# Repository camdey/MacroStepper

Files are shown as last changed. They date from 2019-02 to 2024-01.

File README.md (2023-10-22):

# MacroStepper v3.0
Author: Cam Dey

Created: 2018-12-18

v2.0: 2020-01-01

v3.0: 2023-10-11 // refactor, introduces breaking changes

The MacroStepper is a fully automated macrophotography rig designed to enable a camera to take photos at precisely incremented steps. The macroStack can work with or without an automated shutter and also in manual mode if the user prefers to control the stepping themselves.

# Schematic
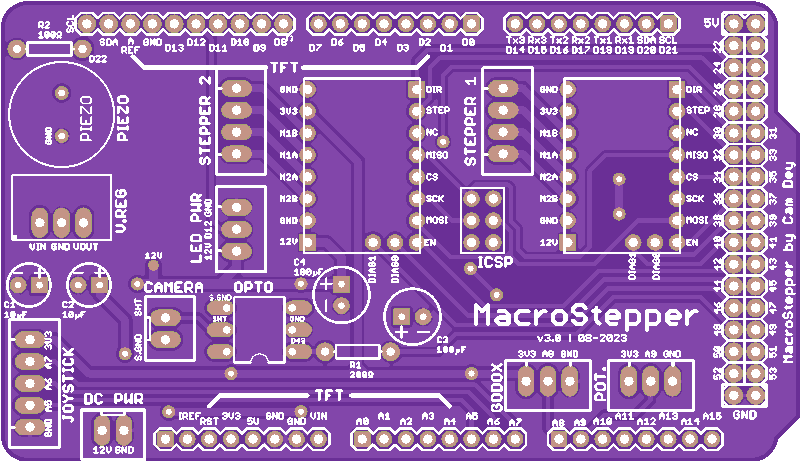
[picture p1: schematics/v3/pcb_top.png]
PCB_top

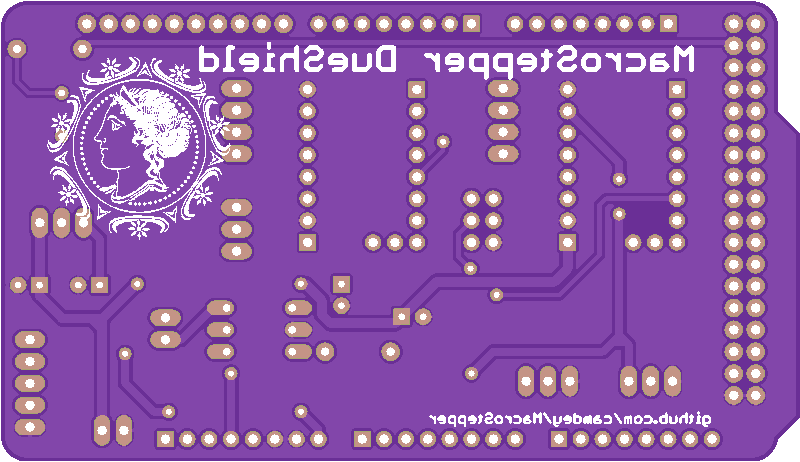
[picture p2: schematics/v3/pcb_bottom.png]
PCB_bottom


# Interface
**Home Screen**
 - House icon: _run homing sequence for the rail, finds min and max positions of the rail_
 - X icon: _clears the settings from the auto mode_
 
**Manual Screen**
 - Step Dist: _press to set distance per movement of the motor_
	 - _value is the distance per movement covered by the rail in millimetres_
 - Step Nr: _number of movements taken in manual mode_
 - Rail Pos: _current position of the camera on the rail_
 - Aperture icon: _press to enable/disable automated shutter_
 - X icon: _press to clear step count_
 - Arrows: _for increment/decrementing the Step Size if enabled or moving the rail forward/back otherwise_

**Auto Screen**
 - Step Dist: _press to set distance per movement of the motor_
	 - _value is the distance per movement covered by the rail in millimetres_
 - Est. Time: _estimated time remaining in autoStack procedure. Takes into account shutter delay and the recycle time of the flash unit_
 - Progress: _number of movements completed out of total number of movements in procedure_
 - Aperture icon: _press to enable/disable automated shutter_
 - Cog icon: _opens the config menu for the auto mode_
 - Play symbol: _used to increment Step Size if enabled, otherwise used for starting the autoStack procedure_
 - Pause symbol: _used to decrement Step Size if enabled, otherwise used for pausing the autoStack procedure_

**Config Screen**

 - START: _press to set the start position for the autoStack procedure. Will automatically change to current position when enabled, use joystick or arrows to move rail into correct position_
 - END: _press to set the end position for the autoStack procedure. Will automatically change to current position when enabled, use joystick or arrows to move rail into correct position_
 - RUN: _will move the camera rail to the START position, slowly increment through the autoStack range until it reaches the END, and then move back to the START position_
 - Clock symbol: _press to change the shutter delay between taking photos after each movement of the stepper motor_
 - Arrows: _used to increment/decrement shutter delay or move the position of the rail_

# Functionality
**Flash/Shutter Control**
The camera shutter is controlled by the Arduino via cable where a HIGH signal is sent to a transistor to short the Shutter and Focus pins of the Sony A6000 to ground. The duration of this signal is determined by an output signal from a PC sync cable. This cable is connected to the output of a Godox X1T-S transmitter. This transmitter sends a LOW signal for several milliseconds when the flash is ready to trigger. When the low signal is received by the Arduino, the shutter line goes LOW and the Shutter and Focus pins are returned to nominal state.

**Distance settings**
The step distance setting refers to the distance travelled by the rail per movement. A movement is the sequence of steps required by the stepper motor to travel the set distance. The default distance per step in my case was 25μm, calculated by the following: screw pitch / steps per revolution / gear reduction. My rail had a 1mm pitch and 1:2 gear reduction, while the motor takes 200 steps per revolution.

If the step size is set to 100μm, this equates to four steps at 25μm each. The sequence of these four steps is termed a movement in this project.

**AutoStack Procedure**
The autoStack procedure will increment a range by a given number of movements, determined by the step distance and the start and end positions determined by the user. With a 100μm step distance and 180 steps required to go from the start position to the end position, 45 (180/4) movements are required and thus 45 photos will be taken. The procedure can be paused or reset at any stage and after completion the procedure can be restarted. Both step distance and the end position can be changed during the procedure once paused.

# Macrophotography

## What is focus stacking?

Focus stacking is a method popular within the field of macrophotography where multiple photos of the same subject are taken at different focus depths and then merged together with software. This enables a macro lens with a shallow depth of field to produce an image of a subject that is fully in focus, even if the subject is physically longer than the depth of field of the lens.

## What do you need for Macrophotography?

While you can create a focus stack just with handheld photos taken at different distances from the subject, typically a **macro rail** is used to help with this process. A macro rail allows you to move a camera attached to a platform by very specific distances along a fixed rail or slide. By turning a handle or knob of the macro rail, the camera can be incremented along the rail by distances as small as 25μm or as large as the rail is long.

**Macro Rail**
For this project, you will need a macro rail that can be attached to a stepper motor. Many commercially available macro rails can be retrofitted with a pinion gear to accept a belt, which is in turn attached to a pinion gear on a stepper motor. Other macro rails are designed to interface directly with a stepper motor, especially those designed to be used for CNC machines or 3D printing.

**Stepper Motor**
A stepper motor is required to move the macro rail automatically. You can do this manually, and many do, but after awhile you get sick of the repetitive process of "move camera rail, take photo, move camera rail, take photo".

There are many types of stepper motors available but for this project I would recommend one in the NEMA 17 form factor with either 200 (1.8°) or 400 (0.9°) steps per revolution and between 1A and 2A current rating. The current rating is important for the load the stepper motor can move and hold but it is not the only determiner of this. A motor with a holding torque of at least 3kg-cm should be adequate.

The voltage of the motor is less important as you can supply more voltage than the rated voltage of the motor. More supply voltage typically equals a faster motor.

**Camera and Lens**
Any DSLR or mirrorless camera will be suitable. A macro lens of your choosing is also sufficient.

**Lighting**
I would recommend buying a flash for your camera, preferably wireless. Macrophotography often deals with very low amounts of light and high apertures so a flash is particularly useful. This project is designed to work with the shutter of a Sony multi-terminal port for triggering the shutter and a PC sync cable for detecting the output signal of the flash being triggered but either of these can be changed to the communication methods required for your camera and flash.

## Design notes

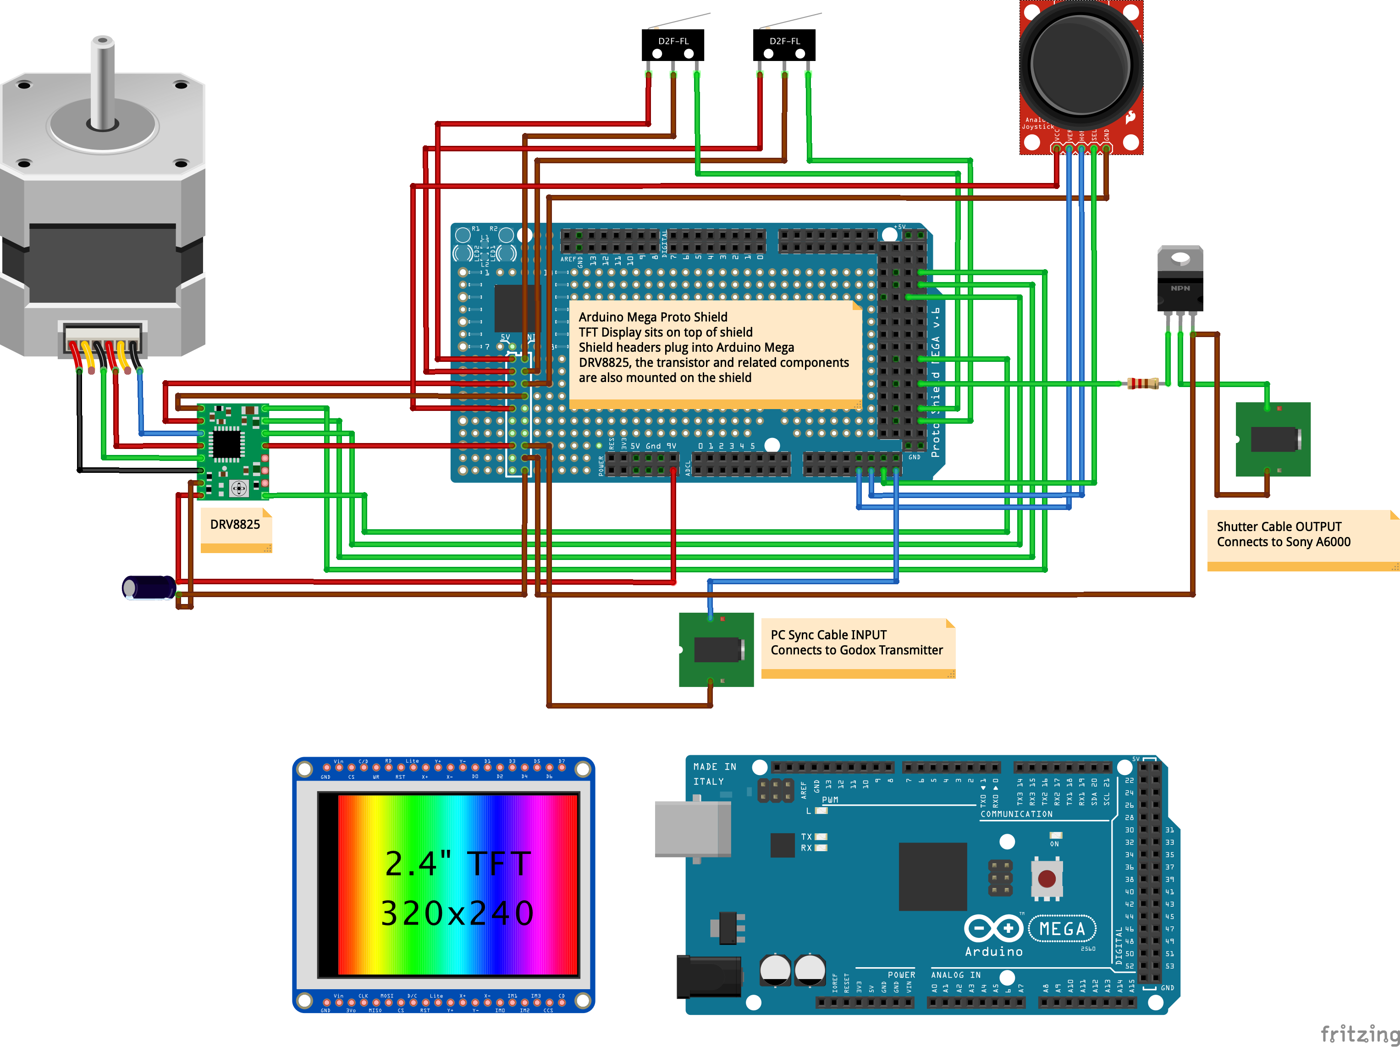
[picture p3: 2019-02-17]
MacroStepper_schematic.png

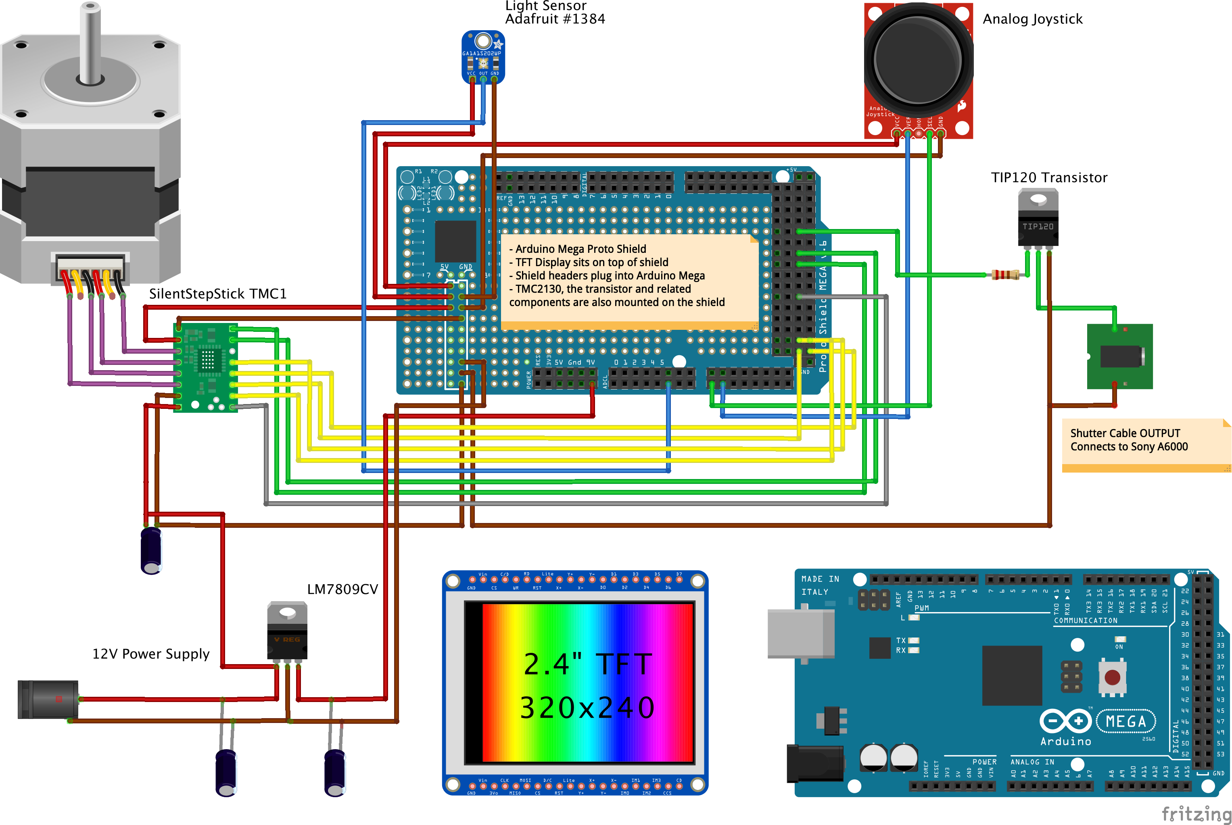
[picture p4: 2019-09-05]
MacroStepper Schematic [Update].png

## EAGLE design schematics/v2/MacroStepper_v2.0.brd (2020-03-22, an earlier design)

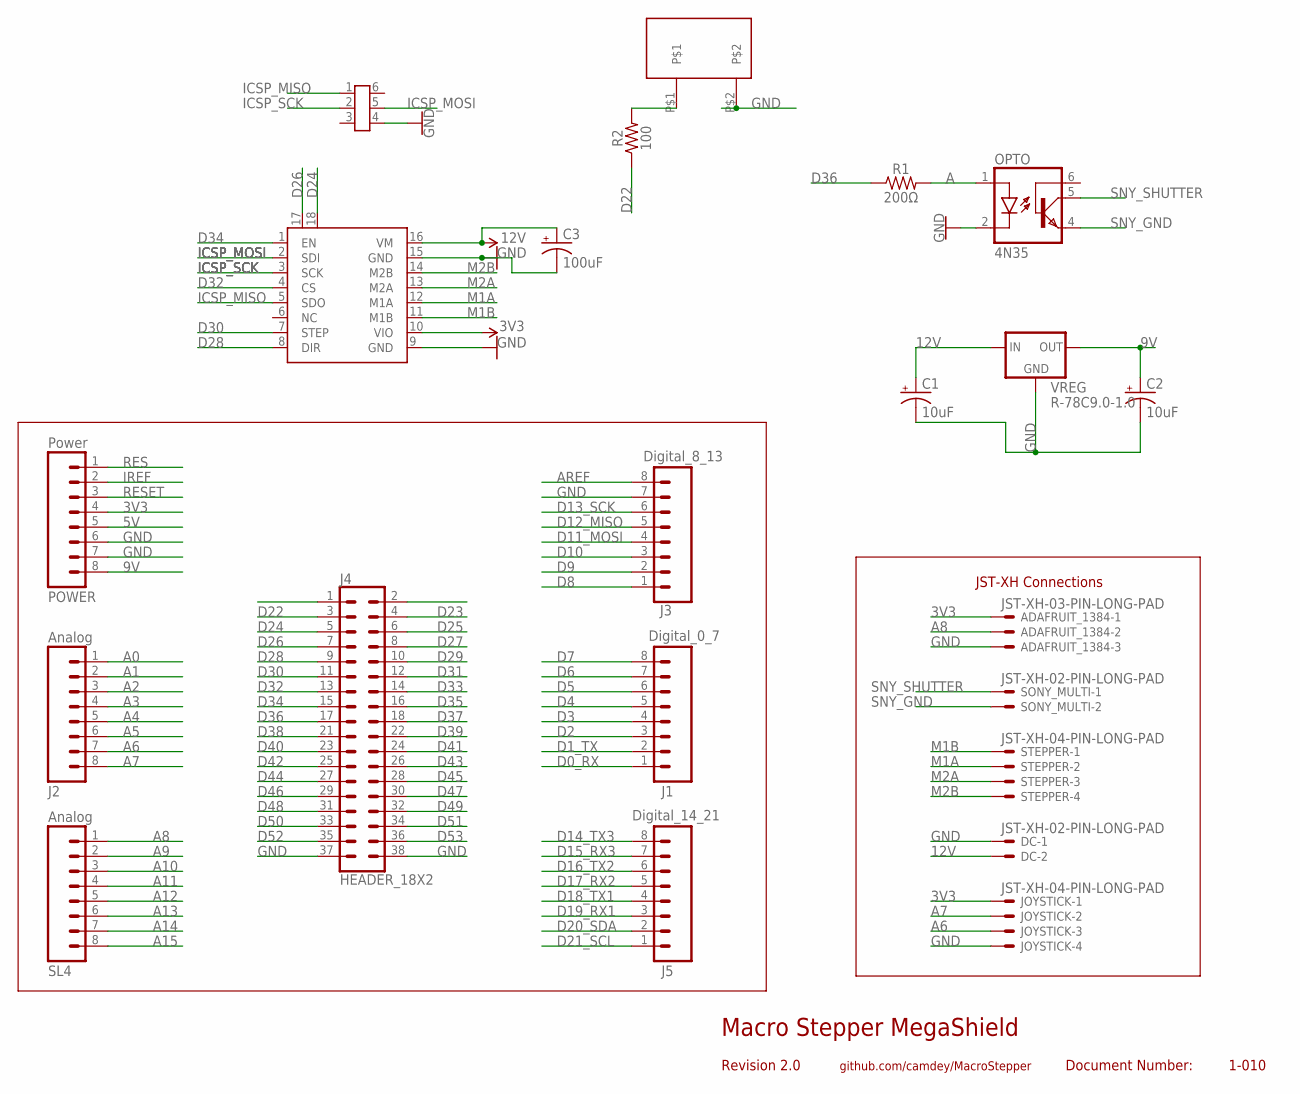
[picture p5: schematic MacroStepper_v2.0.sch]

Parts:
ADAFRUIT_1384: JST-XH-03-PIN-LONG-PAD; JST-XH-03-PACKAGE-LONG-PAD
C1, C2: 10uF; CPOL-RADIAL-2.5MM-5MM
C3: 100uF; CPOL-RADIAL-2.5MM-6.5MM
DC: JST-XH-02-PIN-LONG-PAD; JST-XH-02-PACKAGE-LONG-PAD
ICSP: MEGA_ICSP
J1: Digital_0_7; 1X08
J2: Analog; 1X08
J3: Digital_8_13; 1X08
J4: HEADER_18X2; 2X18
J5: Digital_14_21; 1X08
JOYSTICK: JST-XH-04-PIN-LONG-PAD; JST-XH-04-PACKAGE-LONG-PAD
OPTO: 4N35; DIL06
PIEZO: PS1240P02BT
POWER: Power; 1X08
R1: 200Ω; AXIAL-0.3
R2: 100; AXIAL-0.3
SL4: Analog; 1X08
SONY_MULTI: JST-XH-02-PIN-LONG-PAD; JST-XH-02-PACKAGE-LONG-PAD
STEPPER: JST-XH-04-PIN-LONG-PAD; JST-XH-04-PACKAGE-LONG-PAD
TMC2130: TMC2130; DIL16
VREG: R-78C9.0-1.0; SIP3

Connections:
3V3: ADAFRUIT_1384.1, JOYSTICK.1, POWER.4, TMC2130.10 (VIO)
5V: POWER.5
9V: C2.1 (+), POWER.8, VREG.3 (OUT)
12V: C1.1 (+), C3.1 (+), DC.2, TMC2130.16 (VM), VREG.1 (IN)
A: OPTO.1 (A), R1.P$2 (2)
A0: J2.1
A1: J2.2
A2: J2.3
A3: J2.4
A4: J2.5
A5: J2.6
A6: J2.7, JOYSTICK.3
A7: J2.8, JOYSTICK.2
A8: ADAFRUIT_1384.2, SL4.1
A9: SL4.2
A10: SL4.3
A11: SL4.4
A12: SL4.5
A13: SL4.6
A14: SL4.7
A15: SL4.8
AREF: J3.8
D0_RX: J1.1
D1_TX: J1.2
D2: J1.3
D3: J1.4
D4: J1.5
D5: J1.6
D6: J1.7
D7: J1.8
D8: J3.1
D9: J3.2
D10: J3.3
D11_MOSI: J3.4
D12_MISO: J3.5
D13_SCK: J3.6
D14_TX3: J5.8
D15_RX3: J5.7
D16_TX2: J5.6
D17_RX2: J5.5
D18_TX1: J5.4
D19_RX1: J5.3
D20_SDA: J5.2
D21_SCL: J5.1
D22: J4.3 (D22), R2.P$1 (1)
D23: J4.4 (D23)
D24: J4.5 (D24), TMC2130.18 (DIAG1)
D25: J4.6 (D25)
D26: J4.7 (D26), TMC2130.17 (DIAG0)
D27: J4.8 (D27)
D28: J4.9 (D28), TMC2130.8 (DIR)
D29: J4.10 (D29)
D30: J4.11 (D30), TMC2130.7 (STEP)
D31: J4.12 (D31)
D32: J4.13 (D32), TMC2130.4 (CS)
D33: J4.14 (D33)
D34: J4.15 (D34), TMC2130.1 (EN)
D35: J4.16 (D35)
D36: J4.17 (D36), R1.P$1 (1)
D37: J4.18 (D37)
D38: J4.21 (D38)
D39: J4.22 (D39)
D40: J4.23 (D40)
D41: J4.24 (D41)
D42: J4.25 (D42)
D43: J4.26 (D43)
D44: J4.27 (D44)
D45: J4.28 (D45)
D46: J4.29 (D46)
D47: J4.30 (D47)
D48: J4.31 (D48)
D49: J4.32 (D49)
D50: J4.33 (D50)
D51: J4.34 (D51)
D52: J4.35 (D52)
D53: J4.36 (D53)
GND: ADAFRUIT_1384.3, C1.2 (-), C2.2 (-), C3.2 (-), DC.1, ICSP.4 (GND), J3.7, J4.37 (GND), J4.38 (GND), JOYSTICK.4, OPTO.2 (C), PIEZO.P$2, POWER.6, POWER.7, TMC2130.9 (GND), TMC2130.15 (GND), VREG.2 (GND)
ICSP_MISO: ICSP.1 (MISO), TMC2130.5 (SDO)
ICSP_MOSI: ICSP.5 (MOSI), TMC2130.2 (SDI)
ICSP_SCK: ICSP.2 (SCK), TMC2130.3 (SCK)
IREF: POWER.2
M1A: STEPPER.2, TMC2130.12 (M1A)
M1B: STEPPER.1, TMC2130.11 (M1B)
M2A: STEPPER.3, TMC2130.13 (M2A)
M2B: STEPPER.4, TMC2130.14 (M2B)
unnamed: PIEZO.P$1, R2.P$2 (2)
RES: POWER.1
RESET: POWER.3
SNY_GND: OPTO.4 (EMI), SONY_MULTI.2
SNY_SHUTTER: OPTO.5 (COL), SONY_MULTI.1

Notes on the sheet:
JST-XH Connections
Macro Stepper MegaShield
Revision 2.0
github.com/camdey/MacroStepper
Document Number:
1-010

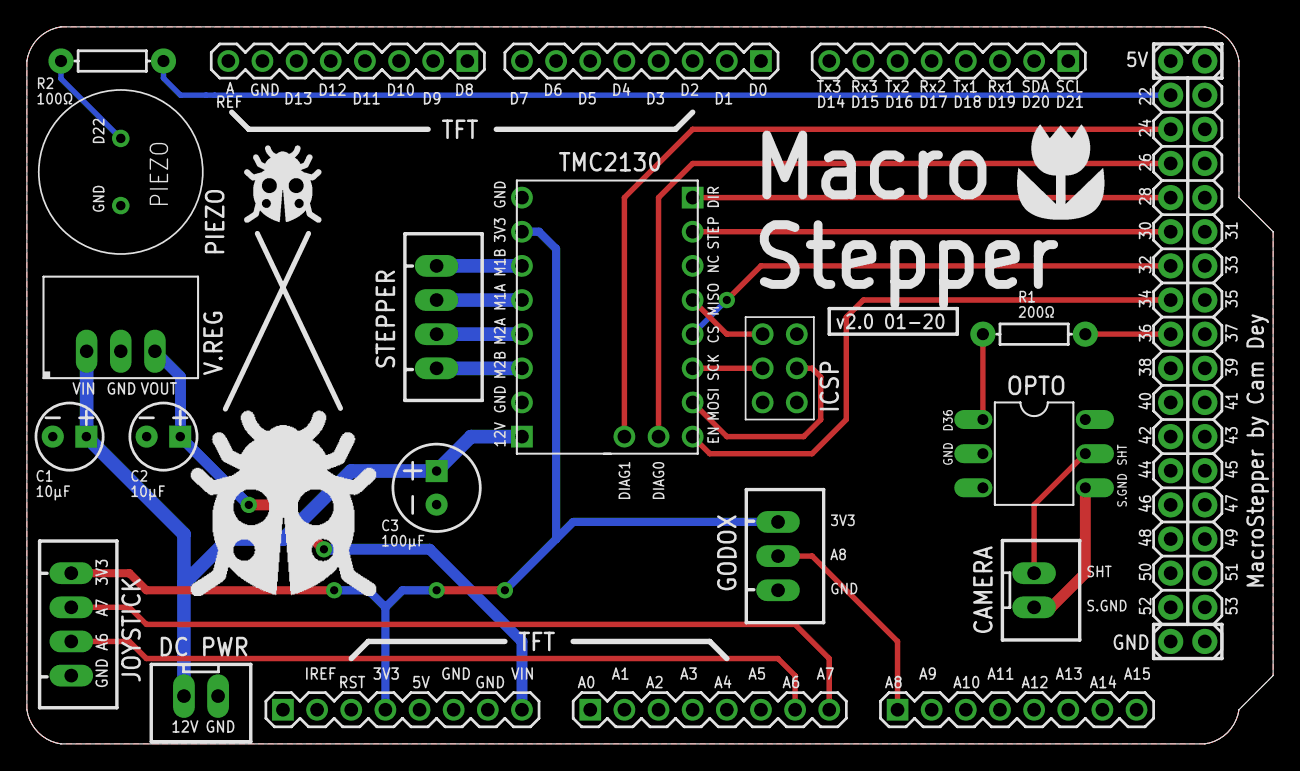
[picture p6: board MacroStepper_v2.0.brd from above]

Board: 2 copper layers, 92.7 x 53.3 mm, 22 parts (0 on the bottom side), 26 nets.

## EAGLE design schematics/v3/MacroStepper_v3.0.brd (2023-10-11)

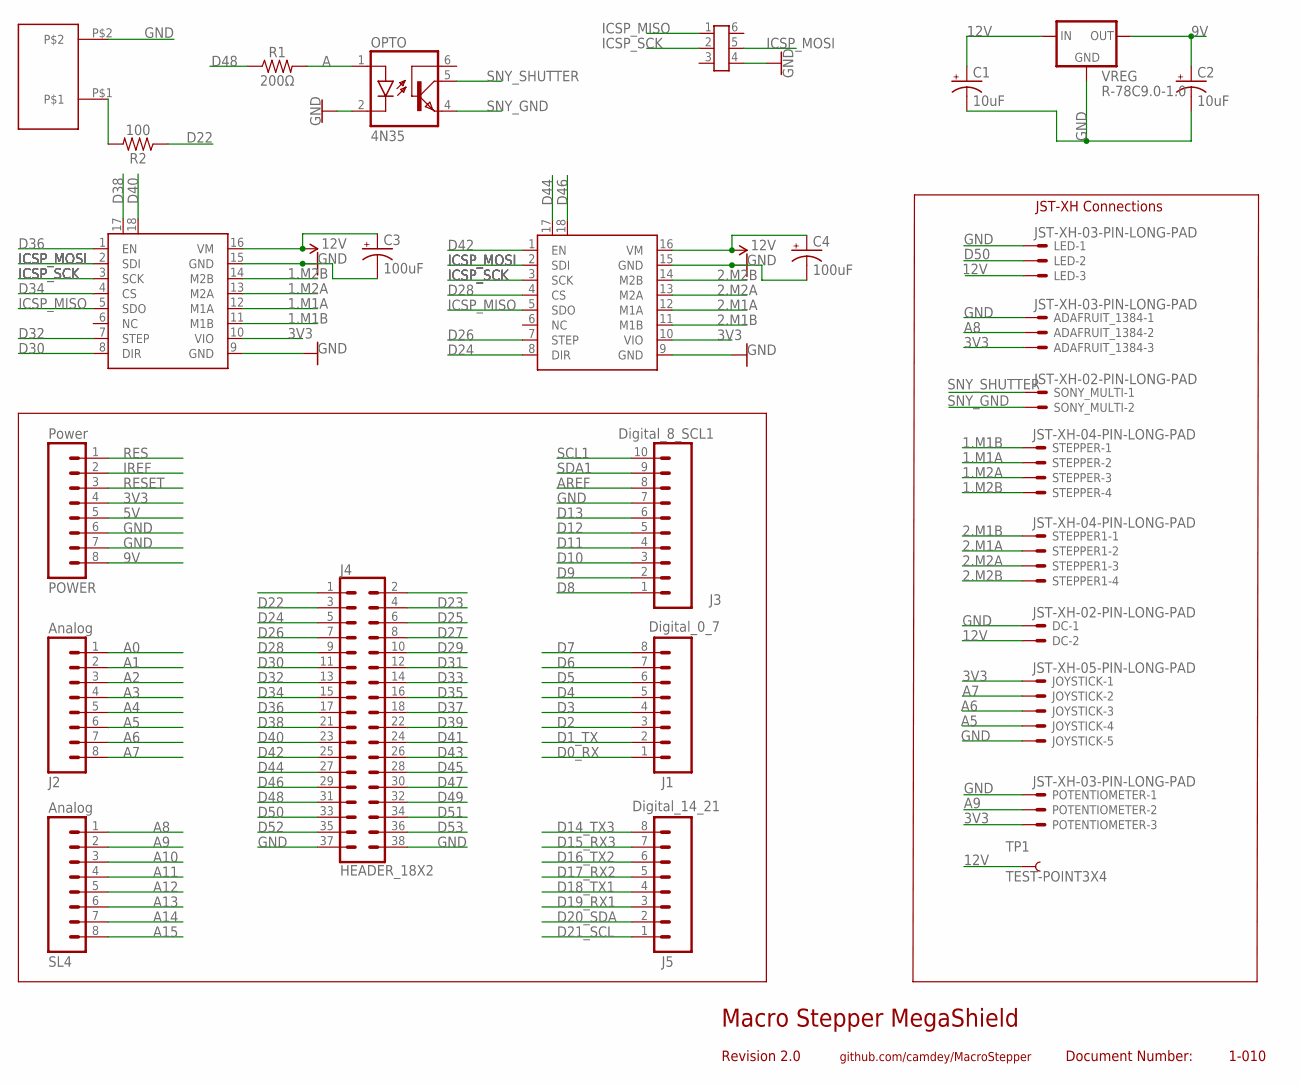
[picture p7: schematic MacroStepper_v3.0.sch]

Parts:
ADAFRUIT_1384: JST-XH-03-PIN-LONG-PAD; JST-XH-03-PACKAGE-LONG-PAD
C1, C2: 10uF; CPOL-RADIAL-2.5MM-5MM
C3, C4: 100uF; CPOL-RADIAL-2.5MM-6.5MM
DC: JST-XH-02-PIN-LONG-PAD; JST-XH-02-PACKAGE-LONG-PAD
ICSP: MEGA_ICSP
J1: Digital_0_7; 1X08
J2: Analog; 1X08
J3: Digital_8_SCL1; 1X10
J4: HEADER_18X2; 2X18
J5: Digital_14_21; 1X08
JOYSTICK: JST-XH-05-PIN-LONG-PAD; JST-XH-05-PACKAGE-LONG-PAD
LED: JST-XH-03-PIN-LONG-PAD; JST-XH-03-PACKAGE-LONG-PAD
OPTO: 4N35; DIL06
PIEZO: PS1240P02BT
POTENTIOMETER: JST-XH-03-PIN-LONG-PAD; JST-XH-03-PACKAGE-LONG-PAD
POWER: Power; 1X08
R1: 200Ω; AXIAL-0.3
R2: 100; AXIAL-0.3
SL4: Analog; 1X08
SONY_MULTI: JST-XH-02-PIN-LONG-PAD; JST-XH-02-PACKAGE-LONG-PAD
STEPPER, STEPPER1: JST-XH-04-PIN-LONG-PAD; JST-XH-04-PACKAGE-LONG-PAD
TMC5160_1, TMC5160_2: TMC2130; DIL16
TP1: TEST-POINT3X4; PAD.03X.04
VREG: R-78C9.0-1.0; SIP3

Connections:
1.M1A: STEPPER.2, TMC5160_1.12 (M1A)
1.M1B: STEPPER.1, TMC5160_1.11 (M1B)
1.M2A: STEPPER.3, TMC5160_1.13 (M2A)
1.M2B: STEPPER.4, TMC5160_1.14 (M2B)
2.M1A: STEPPER1.2, TMC5160_2.12 (M1A)
2.M1B: STEPPER1.1, TMC5160_2.11 (M1B)
2.M2A: STEPPER1.3, TMC5160_2.13 (M2A)
2.M2B: STEPPER1.4, TMC5160_2.14 (M2B)
3V3: ADAFRUIT_1384.3, JOYSTICK.1, POTENTIOMETER.3, POWER.4, TMC5160_1.10 (VIO), TMC5160_2.10 (VIO)
5V: POWER.5
9V: C2.1 (+), POWER.8, VREG.3 (OUT)
12V: C1.1 (+), C3.1 (+), C4.1 (+), DC.2, LED.3, TMC5160_1.16 (VM), TMC5160_2.16 (VM), TP1.P$1, VREG.1 (IN)
A: OPTO.1 (A), R1.P$2 (2)
A0: J2.1
A1: J2.2
A2: J2.3
A3: J2.4
A4: J2.5
A5: J2.6, JOYSTICK.4
A6: J2.7, JOYSTICK.3
A7: J2.8, JOYSTICK.2
A8: ADAFRUIT_1384.2, SL4.1
A9: POTENTIOMETER.2, SL4.2
A10: SL4.3
A11: SL4.4
A12: SL4.5
A13: SL4.6
A14: SL4.7
A15: SL4.8
AREF: J3.8
D0_RX: J1.1
D1_TX: J1.2
D2: J1.3
D3: J1.4
D4: J1.5
D5: J1.6
D6: J1.7
D7: J1.8
D8: J3.1
D9: J3.2
D10: J3.3
D11: J3.4
D12: J3.5
D13: J3.6
D14_TX3: J5.8
D15_RX3: J5.7
D16_TX2: J5.6
D17_RX2: J5.5
D18_TX1: J5.4
D19_RX1: J5.3
D20_SDA: J5.2
D21_SCL: J5.1
D22: J4.3 (D22), R2.P$1 (1)
D23: J4.4 (D23)
D24: J4.5 (D24), TMC5160_2.8 (DIR)
D25: J4.6 (D25)
D26: J4.7 (D26), TMC5160_2.7 (STEP)
D27: J4.8 (D27)
D28: J4.9 (D28), TMC5160_2.4 (CS)
D29: J4.10 (D29)
D30: J4.11 (D30), TMC5160_1.8 (DIR)
D31: J4.12 (D31)
D32: J4.13 (D32), TMC5160_1.7 (STEP)
D33: J4.14 (D33)
D34: J4.15 (D34), TMC5160_1.4 (CS)
D35: J4.16 (D35)
D36: J4.17 (D36), TMC5160_1.1 (EN)
D37: J4.18 (D37)
D38: J4.21 (D38), TMC5160_1.17 (DIAG0)
D39: J4.22 (D39)
D40: J4.23 (D40), TMC5160_1.18 (DIAG1)
D41: J4.24 (D41)
D42: J4.25 (D42), TMC5160_2.1 (EN)
D43: J4.26 (D43)
D44: J4.27 (D44), TMC5160_2.17 (DIAG0)
D45: J4.28 (D45)
D46: J4.29 (D46), TMC5160_2.18 (DIAG1)
D47: J4.30 (D47)
D48: J4.31 (D48), R1.P$1 (1)
D49: J4.32 (D49)
D50: J4.33 (D50), LED.2
D51: J4.34 (D51)
D52: J4.35 (D52)
D53: J4.36 (D53)
GND: ADAFRUIT_1384.1, C1.2 (-), C2.2 (-), C3.2 (-), C4.2 (-), DC.1, ICSP.4 (GND), J3.7, J4.37 (GND), J4.38 (GND), JOYSTICK.5, LED.1, OPTO.2 (C), PIEZO.P$2, POTENTIOMETER.1, POWER.6, POWER.7, TMC5160_1.9 (GND), TMC5160_1.15 (GND), TMC5160_2.9 (GND), TMC5160_2.15 (GND), VREG.2 (GND)
ICSP_MISO: ICSP.1 (MISO), TMC5160_1.5 (SDO), TMC5160_2.5 (SDO)
ICSP_MOSI: ICSP.5 (MOSI), TMC5160_1.2 (SDI), TMC5160_2.2 (SDI)
ICSP_SCK: ICSP.2 (SCK), TMC5160_1.3 (SCK), TMC5160_2.3 (SCK)
IREF: POWER.2
unnamed: PIEZO.P$1, R2.P$2 (2)
RES: POWER.1
RESET: POWER.3
SCL1: J3.10
SDA1: J3.9
SNY_GND: OPTO.4 (EMI), SONY_MULTI.2
SNY_SHUTTER: OPTO.5 (COL), SONY_MULTI.1

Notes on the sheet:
JST-XH Connections
Macro Stepper MegaShield
Revision 2.0
github.com/camdey/MacroStepper
Document Number:
1-010

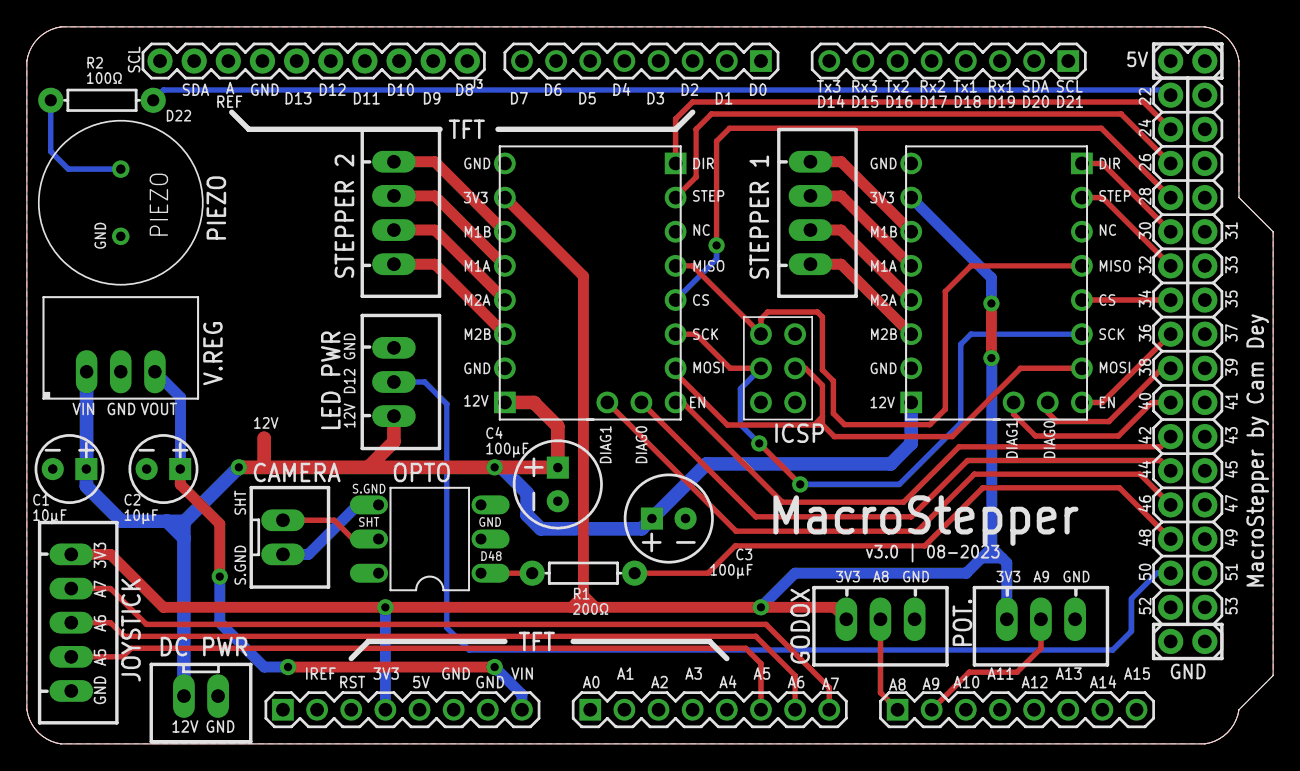
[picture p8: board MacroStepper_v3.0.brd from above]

Board: 2 copper layers, 92.7 x 53.3 mm, 29 parts (1 on the bottom side), 39 nets.

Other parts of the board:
U$1: ARTEMIS_LOGO_LARGE

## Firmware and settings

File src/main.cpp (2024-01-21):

// ********* Macro Stepper v2.2 *********
// *** AUTHOR: Cam Dey
// *** DATE: 2019-01-27
// *** UPDATED: 2023-08-26
// **************************************

// Macro Stepper was written to automate the focus stacking procedure commonly used
// in macrophotography. The manual mode allows the user to input the distance to travel
// per step (here called a "Movement") and whether to trigger the camera via shutter cable
// or not. The automatic mode ("AutoStack") will make a specified number of Movements
// based on the user inputted "Start" and "End" points, as well as the distance specified
// per Movement. A shutter delay can also be specified so that there is a pause before each Movement.
// This delay can be used to allow your camera flash time to recharge before the next shot.

// ----- DEFINITIONS ----- //
// STEP             = one microstep step of the stepper stepper motor
// MOVEMENT 		= one full movement of linear rail by specified distance, consisting of multiple steps
// PROCEDURE 		= one completed stack procedure, consisting of multiple movements
// DISTANCE 		= distance travelled per movement = number of steps per movement * 0.0025mm
// MANUAL MODE      = user input required to step motor by specified distance
// AUTOSTACK        = automatic mode, stepper completes procedure without further input

#include "Arduino.h"
#include "Adafruit_GFX.h"                   // core graphics library
#include "TouchScreen.h"                    // touchscreen library
#include "MCUFRIEND_kbv.h"                  // display driver for IL9481
#include "TMCStepper.h"
#include "TimerFreeTone.h"                  // produces beep tone for piezo
#include "gfxButton.h"                      // my library for adding/controlling TFT buttons
// project definitions and functions
#include "JoystickControl.h"                // joystick control functions
#include "CameraControl.h"                 // functions relating to the camera shutter and flash
#include "StepperControl.h"                 // functions for controlling the stepper motor
#include "LedControl.h"
#include "AutoStack.h"                      // AutoStack class and methods
#include "Photo360.h"
#include "Video360.h"
#include "VariableDeclarations.h"           // external variable declarations
#include "UserInterface.h"
#include "StatusEnums.h"                    // enums containing statuses for various routines, namespace routines::
#include "Piezo.h"
#include "menu/UI-Home.h"
#include "menu/UI-Stack.h"
#include "menu/UI-Orbis.h"
#include "menu/UI-Video360.h"
#include "menu/UI-Photo360.h"
#include "menu/UI-Photo360Config.h"
#include "menu/UI-Manual.h"
#include "menu/UI-Target.h"
#include "menu/UI-Flash.h"
#include "menu/UI-Auto.h"
#include "menu/UI-AutoConfig.h"
#include "Wire.h"
#include "SdFat.h"


TouchScreen             ts = TouchScreen(XP, YP, XM, YM, 300);
TMC5160Stepper_Ext      stepper1(CS_1_PIN, R_1_SENSE);
TMC5160Stepper_Ext      stepper2(CS_2_PIN, R_2_SENSE);
MCUFRIEND_kbv           tft;
gfxButton               btn;
AutoStack               stack(stepper1);
Photo360                photo360(stepper2);
Video360                video360(stepper2);
CameraControl           camera(SHUTTER_PIN, FLASH_SENSOR_PIN);
Joystick                xStick(stepper1, XSTICK_PIN, ZSTICK_PIN);
Joystick                rStick(stepper2, RSTICK_PIN, ZSTICK_PIN);
ledLight                led(LED_PIN, POT_PIN);
UserInterface           ui;
SdFat                   SD;
Piezo                   piezo;


// ***** --- MAIN PROGRAM --- ***** //
void setup(void) {
    Serial.begin(250000);
	SPI.begin();
    tft.reset();

    if (!SD.begin(SD_CS_PIN)) {
        Serial.println("initialization failed!");
    }

    pinMode(PIEZO_PIN, OUTPUT);
	pinMode(EN_1_PIN, OUTPUT);
    pinMode(EN_2_PIN, OUTPUT);
    pinMode(CS_1_PIN, OUTPUT);
    pinMode(CS_2_PIN, OUTPUT);
    pinMode(LED_PIN, OUTPUT);
    // declare analog pin as digital input
    pinMode(ZSTICK_PIN, INPUT_PULLUP);    // pullup needed for consistent readings
    pinMode(SHUTTER_PIN, OUTPUT);

	uint16_t identifier = tft.readID();
	tft.begin(identifier);
	tft.setRotation(3);
    ui.screenRotated(false);

    led.setBrightness(0);

	stepper1.initDriver(1400, NR_MICROSTEPS, 1, EN_1_PIN, CS_1_PIN); //1400
    stepper2.initDriver(850, NR_MICROSTEPS, 0, EN_2_PIN, CS_2_PIN);

    stepper1.slaveSelected(false);
    stepper1.enabled(false);
    stepper1.configStealthChop();

    stepper2.slaveSelected(false);
    stepper2.enabled(false);
    rStick.maxVelocity(2000); //set vmax to 2000 for rStick
    
    digitalWrite(SHUTTER_PIN, LOW);

    rStick.restValLower(490);
    rStick.restValUpper(530);

    btn.begin(&tft, &SD);
    btn.setScreenSize(480, 320);

    ui.initButtons(200, 75);
    ui.populateScreen(routines::ui_Home);

    rStick.restValUpper(530);
    rStick.restValLower(490);
}

void loop() {
    // run AutoStack sequence if not paused or inactive
    if (stack.busy()) {
        stack.run();
        // update duration if on Auto screen
        if (ui.activeScreen() == routines::ui_Auto) {
		    auto_screen::estimateDuration();
        }
    }
    // if not running AutoStack, we manually check for camera shutter to see if it needs to be set to low again
    // else if (camera.lastCheckMillis() >= 50) {
    //     if (digitalRead(camera.shutterPin()) == HIGH) {
    //         camera.triggerShutter(false);
    //     }
    //     camera.lastCheckMillis(millis());
    // }
    // take touch reading
    if (millis() - ui.lastCheckMillis() >= 50) {
        ui.readTouchScreen(ui.activeScreen());
        ui.lastCheckMillis(millis());
        // if video360 active, keep updating target so stepper keeps moving
        if (video360.busy()) {
            video360.run();
        }
        if (photo360.busy()) {
            photo360.run();
        }
    }
    // take joystick and limit switch reading, put stepper to sleep
    if (millis() - xStick.lastCheckMillis() >= 50) {
        // check joystick for movement if button depressed and not in autoStack or photo360/video360 mode
        if (!stack.busy() && !photo360.busy() && !video360.busy()) {
            int xPos = xStick.readSmoothed();
            int rPos = rStick.readSmoothed();
            // Serial.print("rpos: "); Serial.println(rPos);
            if ((xPos >= xStick.restValUpper() || xPos <= xStick.restValLower()) && xStick.buttonActive()) {
                xStick.motion(true);
            }
            else if ((rPos >= rStick.restValUpper() || rPos <= rStick.restValLower()) && !rStick.buttonActive()) {
                rStick.motion(false);
            }
        }
    //     // sleep if stepper inactive, update position on manual screen
    //     if (stepper1.reachedTarget() && stepper1.enabled() && stack.status() == routines::inactive) {
    //         stepper1.enabled(false); // disable stepper
    //     }
    //     // sleep if stepper inactive, update position on manual screen
    //     if (stepper2.reachedTarget() && stepper2.enabled() && photo360.status() == routines::inactive) {
    //         stepper2.enabled(false); // disable stepper
    //     }
	// 	// update flashSensorValue if on Flash screen
		if (ui.activeScreen() == routines::ui_Flash && (ui.canEdit(routines::btn_flashOff) || ui.canEdit(routines::btn_flashOn))) {
			flash_screen::updateFlashSensorValue();
		}
        xStick.lastCheckMillis(millis());
    }

    if (millis() - led.lastCheckMillis() >= 50) {
        led.updateBrightness();
        // Serial.print("led: "); Serial.println(led.convertToPWM(led.readDimmer()));
    }
}

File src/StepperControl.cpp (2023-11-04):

#include <Arduino.h>
#include "VariableDeclarations.h"
#include "StepperControl.h"
#include "StepperControl.h"
#include "AutoStack.h"
#include "CameraControl.h"
#include "UserInterface.h"
#include "menu/UI-Auto.h"
#include "menu/UI-AutoConfig.h"
#include "menu/UI-Global.h"
#include "menu/UI-Photo360.h"

TMC5160Stepper_Ext::TMC5160Stepper_Ext(uint16_t pinCS, float RS, int8_t link) : TMC5160Stepper(pinCS, RS, link) {};

void TMC5160Stepper_Ext::initDriver(uint16_t rmsCurrent, uint16_t nrMicrosteps, bool shaftDirection, int pinEN, int pinCS) {
    enablePin(pinEN);
    chipSelectPin(pinCS);
    begin();
    slaveSelected(true);
    // 23HM22-2804S: max 1900rms, stepper rated for 2.8A
    // SY42STH47-1206A: max 850rms, stepper rated for 1.2A
    rms_current(rmsCurrent); 
    microsteps(nrMicrosteps);
    shaft(shaftDirection); // inverse shaft, large target moves away from rear, small target moves towards rear
    slaveSelected(false);
}


void TMC5160Stepper_Ext::configStealthChop() {
    GCONF();
    en_pwm_mode(true);
    en_softstop(true);
    PWMCONF();
    pwm_autoscale(true);                            // Needed for stealthChop
    pwm_autograd(true);
    TZEROWAIT(5000);                                // wait time before next movement, approx 300ms, range 0 - 65,536
    TPOWERDOWN(10);
    TPWMTHRS(0);                                    // TSTEP ≥ TPWMTHRS: StealthChop enabled, DcStep disabled
    TCOOLTHRS(0);                                   // TCOOLTHRS ≥ TSTEP ≥ THIGH: CoolStep enabled, StealthChop PWM disabled.
                                                    // TCOOLTHRS ≥ TSTEP: Stop on stall enabled.
    THIGH(100);                                     // TSTEP ≤ THIGH: CoolStep disabled, StealthChop PWM mode disabled. Stall Detection uses DcStep
    VDCMIN(0);                                      // |VACT| ≥ VDCMIN ≥ 256: same as if THIGH exceeded, DcStep auto commutation
    CHOPCONF();
    toff(5);                                        // General enable for motorm driver, 0 = off, >= 1 driver enabled. Value doesn't affect stealthChop
    hstrt(0);
    hend(0);
    tbl(2);                                         // comparator blank time
    chm(0);                                         // 0 = spreadCycle chopper mode (1 = const. off time)
    vhighchm(false);
    vhighfs(false);
    IHOLD_IRUN();
    ihold(5);
    irun(16);
    iholddelay(8);
    RAMPMODE(0);                                    // Positioning mode (using all A, D and V parameters)
    a1(5000);                                       // First acceleration between VSTART and V1
    AMAX(3500);                                     // Second acceleration between V1 and VMAX
    VMAX(STEALTH_CHOP_VMAX);                        // Motion ramp target velocity (VMAX >= VSTART). Can be changed during a motion.
    v1(30000);                                      // First acceleration / deceleration phase treshold velocity
    DMAX(3500);                                     // Deceleration between VMAX and V1
    d1(5000);                                       // Deceleration between V1 and VSTOP
    VSTART(0);                                      // Motor start velocity (VSTOP >= VSTART)
    VSTOP(10);                                      // Motor stop velocity

    // STALLGUARD2 PARAMETERS
    sg_stop(false);                                 // stop by stallguard, disable to release motor after stall event

    stallGuardActive(false);
}


void TMC5160Stepper_Ext::configStallGuard() {
    GCONF();
    en_pwm_mode(true);
    en_softstop(false);
    PWMCONF();
    pwm_autoscale(true);                            // Needed for stealthChop
    pwm_autograd(true);
    TZEROWAIT(10000);                               // wait time before next movement, approx 300ms, range 0 - 65,536
    TPOWERDOWN(0b00);
    TPWMTHRS(0);                                    // TSTEP ≥ TPWMTHRS: StealthChop enabled, DcStep disabled
    TCOOLTHRS(400);                                 // TCOOLTHRS ≥ TSTEP ≥ THIGH: CoolStep enabled, StealthChop PWM disabled.
                                                    // TCOOLTHRS ≥ TSTEP: Stop on stall enabled.
    THIGH(0);                                       // TSTEP ≤ THIGH: CoolStep disabled, StealthChop PWM mode disabled. Stall Detection uses DcStep
    VDCMIN(0);                                      // |VACT| ≥ VDCMIN ≥ 256: same as if THIGH exceeded, DcStep auto commutation
    CHOPCONF();
    toff(5);                                        // General enable for motorm driver, 0 = off, >= 1 driver enabled. Value doesn't affect stealthChop
    hstrt(0);
    hend(0);
    tbl(2);                                         // comparator blank time
    chm(0);                                         // 0 = spreadCycle chopper mode (1 = const. off time)
    vhighchm(false);
    vhighfs(false);
    IHOLD_IRUN();
    ihold(5);
    irun(16);
    iholddelay(8);
    RAMPMODE(0);                                    // Positioning mode (using all A, D and V parameters)
    a1(1000);                                       // First acceleration between VSTART and V1
    AMAX(800);                                      // Second acceleration between V1 and VMAX
    VMAX(50000);                                    // Motion ramp target velocity (VMAX >= VSTART). Can be changed during a motion.
    v1(30000);                                      // First acceleration / deceleration phase treshold velocity
    DMAX(1200);                                     // Deceleration between VMAX and V1
    d1(1000);                                       // Deceleration between V1 and VSTOP
    VSTART(2);                                      // Motor start velocity (VSTOP >= VSTART)
    VSTOP(12);                                      // Motor stop velocity

    // STALLGUARD2 PARAMETERS
    sg_stop(true);                                  // stop by stallguard, disable to release motor after stall event
    sgt(0);                                         // stallguard sensitivity
    semin(2);                                       // If the StallGuard2 result falls below SEMIN*32, the motor current is increased
    semax(1);                                       // If the StallGuard2 result is equal to or above (SEMIN+SEMAX+1)*32, the motor current becomes decreased to save energy.
    sedn(0b00);                                     // For each 8 StallGuard2 values decrease current down step speed by one

    stallGuardActive(true);
}
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

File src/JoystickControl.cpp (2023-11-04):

#include "StepperControl.h"
#include "JoystickControl.h"
#include "UserInterface.h"
#include "Piezo.h"
#include "menu/UI-Manual.h"
#include "menu/UI-AutoConfig.h"


// calculate new velocity (VMAX) value while using joystick motion
// velocity value is a log-transformation of the joystick position
long Joystick::calculateVelocity(int pos) {
    long velocity;
    int xAdj;

    if (pos < 512) {
        xAdj = pos + 1;                 // prevent taking log of 0
    }
    else if (pos >= 512) {
        xAdj = (1024 - pos);
    }
    xAdj = round(log(xAdj)*100);        // multiply by 100 as value will be truncated to integer
    // 624 = log(512)*100 rounded
    // Serial.print("joystick vel: "); Serial.println(getJoystickMaxVelocity());
    velocity = map(xAdj, 0, 624, maxVelocity(), 0);

    return velocity;
}

/******************************************************************
Take 10 readings form the joystick X axis during setup and average
the result. This becomes the resting value for the joystick. If
out of the estimated range (500, 524), set at 512 to be safe.
Add/substract 10 to this resting value to get an upper and lower
bound for detecting movement. Also record difference between the
resting value and ideal mid-point (511.5) to offset pos readings
by in other functions that use this variable.
******************************************************************/
void Joystick::calibrateRestPosition() {
    int numReadings = 10;
    int sumReadings = 0;
    restValDiff(0); // ensure reset to 0 when this function is called

    for (int xth_reading = 0; xth_reading < numReadings; xth_reading++) {
        int pos = read();
        sumReadings += pos; // add reading to total
        delay(20); // wait 20ms
    }

    restVal((sumReadings / numReadings) + 0.5);  // "round" to nearest whole number

    // if restVal() below/above these values, set at middle point to be safe
    if (restVal() < 500 || restVal() > 524) {
        restVal(512);
    }
    restValDiff(restVal() + 10);
    restValLower(restVal() - 10);
    restValDiff(512 - restVal());
}


/******************************************************************
Function for moving the stepper via joystick control on the X axis.
Re-enables stepper if previously disabled and then checks to make
sure the joystick values are still in the operation range.    If the
rail has been homed, it will prevent user from allowing rail to
bump into endstops. Every 50ms it checks for new joystick input
values and also adjusts speed based on joystick input position.
For the first 5000 loops of the while() function, a modifier is
used to reduce the initial acceleration of the stepper to control
jerk. After 5000 steps, modifier is redundant and normal speed
control resumes.
******************************************************************/
void Joystick::motion(bool btnTrigger) {
    _stepper.slaveSelected(true);
    _stepper.enabled(true);
    _stepper.readyStealthChop();
    int pos = readSmoothed();
    int dir = getDirection(pos);
    long velocity = calculateVelocity(pos);
    // Serial.print(millis()); Serial.print(" - btnTrig: "); Serial.print(btnTrigger); Serial.print(" - enabled: "); Serial.print(digitalRead(_stepper.enablePin())); Serial.print(" - pos: "); Serial.println(pos);

    while ((pos >= restValUpper() || pos <= restValLower()) && (buttonActive() || !btnTrigger)) {
        // don't allow movement if within 2mm of endstops if homed
        if (_stepper.homed()) {
            if (dir == 0 && _stepper.XACTUAL() <= SAFE_ZONE_BUFFER) {
                Serial.print("WARNING: hit SAFE_ZONE_BUFFER (within 2mm of rear end stop): "); Serial.println(_stepper.XACTUAL());
                piezo.produceTone(4000, 4, 300, 200); 
                break;
            }
            else if (dir == 1 && MAX_RAIL_POSITION - _stepper.XACTUAL() <= SAFE_ZONE_BUFFER) {
                Serial.print("WARNING: hit SAFE_ZONE_BUFFER (within 2mm of front end stop): "); Serial.println(_stepper.XACTUAL());
                piezo.produceTone(4000, 4, 300, 200); 
                break;
            }
        }
    
        // update velocity if more than 100ms since last reading
        if (millis() - lastCheckMillis() >= 100) {
            velocity = calculateVelocity(pos);
            // Serial.print(" | pos: "); Serial.print(pos);
            // Serial.print(" | currentPos: "); Serial.print(_stepper.XACTUAL());
            // Serial.print(" | targetPos: "); Serial.print(_stepper.XTARGET());
            // Serial.print(" | VACTUAL: "); Serial.print(_stepper.VACTUAL());
            // Serial.print(" | velocity: "); Serial.println(velocity);

            // buttonActive();                      // check if button still pressed, no longer needed as the call in the while clause should update automatically
            printNewPositions();                    // print new positions on the display
            lastCheckMillis(millis());
        }
        // set target to move stepper
        if (dir == 0) {
            _stepper.XTARGET(MAX_RAIL_POSITION*-1);
        }
        else if (dir == 1) {
            _stepper.XTARGET(MAX_RAIL_POSITION);
        }
    
        _stepper.targetVelocity(velocity);
        pos = readSmoothed();
    }
    _stepper.targetVelocity(0);                     // bring stepper to a stop
    while (_stepper.VACTUAL() != 0) {}              // wait for stepper to decelerate
    _stepper.XTARGET(_stepper.XACTUAL());           // reset target to actual, call after setting targetVelocity to avoid "bounce"
    printNewPositions();                            // print final positions now that stepper has stopped
    _stepper.targetVelocity(STEALTH_CHOP_VMAX);     // reset VMAX to stealthChop default
    _stepper.slaveSelected(false);
    _stepper.enabled(false);
}


// Print new rail positions depending on what screen and buttons are active
// Called during joystick movement and after joystick movement when stepper has stopped
// otherwise the position values will be out of sync across different fields
void Joystick::printNewPositions() {
    if (ui.activeScreen() == routines::ui_Manual) {                           // if on Manual screen, print new positon
        manual_screen::printPosition();
    }
    else if (ui.activeScreen() == routines::ui_AutoConfig) {                  // else if Auto Config screen, print new position
        autoconfig_screen::printPosition();

        if (ui.canEdit(routines::btn_startPosition)) {
        autoconfig_screen::updateStartPosition();                   // if editing Start position, set start but not end position
        }
        else if (ui.canEdit(routines::btn_endPosition)) {
            autoconfig_screen::updateEndPosition(); 	            // if editing End position, set end but not start position
        }
    }
}
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

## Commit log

2019-01-17 intergrates stepper motor controls from earlier arduino file
2019-01-19 fixes single step functionality, adds adjustable step distance
    [main.cpp]
2019-01-21 starts implementation of macro stepping, adds shutter support, updates rail pos. in manual mode, changes menu design
2019-01-22 change autoscreen menu, fix bugs, implement pause, add progress counter
    [main.cpp]
2019-01-23 adds manual functionality, reset, shutter trigger func, play/pause, bug fixes
    [main.cpp]
2019-01-24 bug fixes, est. time functionality, manaul shutter, etc
    [main.cpp]
2019-01-26 converted all interval/delay variables to unsigned long to fix bug
    [main.cpp]
2019-01-27 bug fixes: reverse step issue, number updates. Added symbols etc
    [main.cpp]
2019-01-28 adds logo, back button symbol, changes limit positions to after push-off
2019-01-29 finished adding symbols, changed button colours
2019-02-17 adds schematic
2019-02-17 update readme with schematic and pinouts
2019-02-25 refactors stepping functions, autostack, fixes manual step bug, sleeping changed to en able pin
    [main.cpp]
2019-06-22 major updates: support for tmc2130, stall detection, remove limit switches, use light sensor for flash recycle
    [main.cpp]
2019-06-29 more bug fixes, new function for updating values on screen
    [StepperControl.cpp, UserInterface.cpp, VariableDeclarations.h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]
2019-06-30 small fixes to est time
    [StepperControl.cpp, VariableDeclarations.h, main.cpp]
2019-06-30 function for handling unexpected light sensor readings
2019-07-15 functionality for preventing jerk when using joystick
    [StepperControl.cpp, StepperControl.h]
2019-07-19 fixed bug with inverted joystick reading exceeding threshold
    [StepperControl.cpp, VariableDeclarations.h, main.cpp]
2019-07-26 implemented pause stack on flash failure, fixed movementsRequired calc.
    [StepperControl.cpp, UserInterface.cpp]
2019-09-05 update schematic
2019-09-05 add new schematic to readme
2020-03-13 test Grand Central + new PCB
2020-03-15 small adjustments for arduino due
2020-03-22 joystic, homing, tft working on Arduino Due
2020-03-22 split joystick into new cpp, fix issue with missing steps in autoStack start, add overshoot function for backlash
    [JoystickControl.cpp, JoystickControl.h, StepperControl.cpp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]
2020-03-22 add eagle files and pcb images
    [MacroStepper_v2.0.brd, MacroStepper_v2.0.sch]
2020-03-22 Update README.md
    add new PCB image, update pinouts
2020-03-23 first implementation of button library
2020-03-24 replace arrows with bitmaps, add tft-main
    [VariableDeclarations.h, main.cpp]
2020-03-25 implement button draw and check routine
2020-04-03 small bug fixes, improvements
    [UserInterface.cpp, VariableDeclarations.h, main.cpp]
2020-04-10 minor bug fixes and cleaning up
    [UI-AutoConfig.cpp]
2020-04-13 small bug fixes, change arrays to array of pointers
    [StepperControl.cpp, UI-AutoConfig.cpp]
2020-04-13 small tweaks and fixes
    [JoystickControl.cpp, VariableDeclarations.h, main.cpp]
2020-06-07 replace joystick functions with tmc5160 compatible functions
    [JoystickControl.cpp, JoystickControl.h, VariableDeclarations.h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]
2020-07-13 add new homing routine, deprecate stepper.()
2020-07-14 test homing
2020-07-15 implement homing for tmc5160
2020-07-15 implement homing and joystick control for tmc5160
2020-07-16 fix joystick issues, tidy up code
    [JoystickControl.cpp, JoystickControl.h, StepperControl.cpp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]
2020-07-18 bug fixes, cleaning up
    [JoystickControl.cpp, StepperControl.cpp, UI-AutoConfig.cpp]
2020-07-19 more refactoring, fix dryRun procedure, reduce global variables, add tone library
    [JoystickControl.cpp, StepperControl.cpp, UI-AutoConfig.cpp]
2020-07-20 more refactoring, bug fixes, code clean up
    [JoystickControl.cpp, StepperControl.cpp, StepperControl.h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]
2020-07-21 fix joystick overshoot and position update synchronisation
    [JoystickControl.cpp, JoystickControl.h, main.cpp]
2020-07-26 fix play/pause bug, add delay after flash
    [JoystickControl.cpp, StepperControl.cpp, VariableDeclarations.h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]
2020-08-15 bug fixes for btn refactor
    [UI-AutoConfig.cpp]
2020-08-16 add global buttons
2020-08-16 implement hidden buttons for play/pause and arrows
2020-08-16 add global button files
2020-10-19 improve flash function, add bulb disable, small bug fixes
    [StepperControl.cpp, UI-AutoConfig.cpp]
2021-06-27 finish orbis implementation, small fixes
    [JoystickControl.cpp, StepperControl.cpp, UI-AutoConfig.cpp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]
2021-06-27 fix button alignment
2023-07-25 small fixes and improvements
    [StepperControl.cpp, UI-Photo360Config.cpp, VariableDeclarations.h]
2023-07-25 update tmc driver registers to reflect new naming
2023-07-28 decrease min. shutter delay and convert it to milliseconds
2023-08-26 initial refactoring to v3 PCB and dual stepper drivers
2023-08-27 extend tmc5160 class, refactor functions to accept instances of stepper
2023-08-27 contuinue refactor, rename driverconfig to stepperconfig
2023-08-27 fix external stepper var
    [StepperControl.cpp, VariableDeclarations.h]
2023-08-27 fix func not setting vmax, cs enable logic
    [JoystickControl.cpp]
2023-09-02 continue refactoring, camera class finished
2023-09-03 add photo360 class, fix remaining errors
    [AutoStack.cpp, AutoStack.h, CameraControl.cpp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]
2023-09-03 fix bugs stemming from ui class refactor
    [JoystickControl.cpp, UI-AutoConfig.cpp, UI-Config.cpp]
2023-09-05 minor refactoring for adding control of 2nd stepper
2023-09-09 fix joystick ctor, slaveSelected mapping
    [JoystickControl.cpp, JoystickControl.h, StepperControl.cpp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]
2023-09-09 fix bug in configstealthchop that meant it was never run
    [JoystickControl.cpp, StepperControl.h, main.cpp]
2023-09-10 add led class, fix bugs in autostack
    [AutoStack.cpp, AutoStack.h, CameraControl.h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]
2023-10-08 fix photo360, implement video360, fix AutoStack bugs
    [AutoStack.cpp, CameraControl.cpp, CameraControl.h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]
2023-10-11 update readme, add new pcb
    [MacroStepper_v2.0.brd, MacroStepper_v2.0.sch]
2023-10-11 add back schematics, update readme img url
    [MacroStepper_v2.0.brd, MacroStepper_v2.0.sch, MacroStepper_v3.0.brd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]
2023-10-14 add suppor fort rgb bitmap buttons
2023-10-21 add new icons, replace old icons, ui tweaks
    [UI-AutoConfig.cpp, UI-Config.cpp, UI-Photo360Config.cpp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]
2023-11-04 add piezo class, minor fixes and upgrades
    [AutoStack.cpp, AutoStack.h, CameraControl.h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]

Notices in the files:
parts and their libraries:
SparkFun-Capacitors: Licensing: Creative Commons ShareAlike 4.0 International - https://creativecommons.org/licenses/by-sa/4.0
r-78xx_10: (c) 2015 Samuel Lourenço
